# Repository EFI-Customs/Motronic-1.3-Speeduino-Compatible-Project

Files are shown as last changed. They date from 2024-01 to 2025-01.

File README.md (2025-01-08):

# Speeduino Compatible BMW ECU's

This is the main repository containing base maps for various BMW engines utilising the Speeduino Compatible PCB's from EFI Customs.

As well as this, you will find documentation on building your own PCB's.

# Base Maps

It is important to note that these base maps are not intended to be a "ready to go" tune. 

These are purely used as a starting point to get your project going without having to go through the time-consuming process of tweaking every setting.

It is also important to verify your timing with a light before you crank your engine with injectors firing, otherwise you may cause some damage to your motor (not good!). 
These base maps have been preset to be 50deg ATDC (After Top Dead Centre, as opposed to the typical Before Top Dead Centre values used in other kinds of standalone ECU's), which seems to be a typical expected value on a stock M20 running factory single ignition coil. 

Lastly, these base maps have been built under the assumption that a MAX992x based VR Conditioner for the crank sensor. As such, the Trigger Edge is set to RISING. If you are running another type of VR Conditioner or you've converted to Hall Effect then please ensure you have checked this setting before cranking. Remember that if you have switched over to a Hall Effect crank sensor then you need to change jumper configuration on the PCB. There is a jumper configuration table located on the silkscreen underneath where the Arduino mounts.

You can also achieve your own base map by using the Speeduino base maps found here: [Official and user contributed base tunes for Speeduino installations](https://github.com/speeduino/Tunes)

## Motronic 1.3 General Information & Observations
These instructions are designed for the V1.7 Motronic 1.3 Board.
For the Motronic 1.3 compatible ECU, please ensure you have done;

### Air Flow Meter (AFM)
Assuming you are keeping your AFM, unplug the AFM connector and add wires to pins 1 & 4 on the plug and connect them to pins 1 & 4 on the AFM. 
Doing so allows us to utilise the factory intake air temperature sensor. 

The reason we need to unplug pins 2 & 3 is because they go to the External MAP and +5V line on the ECU pins 7 and 12 respectively. 
If you do not do this, you will find that your MAP reading will halve, and you will experience signal noise.

If you intend to delete the AFM, you can instead run any generic intake temperature sensor. A very popular one is an Open Element GM IAT sensor. Again, you can just wire this sensor into the factory AFM harness (pins 1 & 4).

### TPS
If you want to start the car without re-wiring the TPS, simply unplug it and manually enter values in the TPS calibration window to spoof readings. 
However, on a full implementation of this board it is highly recommended to convert to an M50 style TPS.

To convert your TPS to the M50 one you need to do the following:

 - Acquire M50 TPS (Part number 13 63 1 721 456)
 - Acquire M50 TPS Adapter 
 - Swap pins 1 (Brown/Blue) and 2 (Brown) on the factory TPS Connector

### Ignition

If you are running factory ignition and you have the cylinder 1 pulse sensor attached (image link here: https://www.r3vlimited.com/board/filedata/fetch?id=7225671) you need to unplug the sensor from the engine harness. 

The Motronic PCB's support individual coil-on-plug for up to 4 cyl engines (needs Cam Position Sensor retrofitted) and wasted-spark for 6-cyl engines. To retrofit a cam sensor you can re-use the cylinder 1 pulse sensor plug on the engine harness side. A MAX9926 VR Conditioner accepts two inputs (crank + cam).

The principle remains similar for both platforms, but we will cover the most common Wasted Spark conversion for an M20.

There are multiple approaches to converting to Wasted Spark, we'll cover the two easiest:

#### Method 1 - Retain the factory coil wiring (black wire and green wire)
The Motronic 1.3 PCB has an external ignition connector for additional channels, for this method you need to add two wires that go from the Ign 2.1 and 3.1 channels on the connector to the respective coils. 
In total, you will have three ignition channel wires and one +12V (green) wire.
The factory black wire will act as channel 1 ignition, 2.1 (PCB) is channel 2 and 3.1 (PCB) is channel 3.

#### Method 2 - Utilise the external connector exclusively
As the title suggests, we either remove or hide the factory black ignition wire and run the 3 channels exclusively from the external ignition connector on the ECU PCB.

Channel 1.1, 2.1 and 3.1 on the PCB are channels 1,2,3 respectively. 
With this method, we still retain the factory green coil wire to provide switched +12V.

#### Ignition wiring continued
We have used a GM V6 Coil Pack with a gutted and re-wired DFI module.

Reference Delphi Coil Pack Part Number: GN10123

Reference Delphi DFI Module Part Number: CM414

Reference DFI Module wiring guide: https://www.e30zone.net/e30wiki/images/9/9a/Gmgutted.jpg

Another wiring reference image: http://i.imgur.com/Q9WdHVS.png

Use a multimeter to ensure you have connected the respective wires to the appropriate pins on the DFI Module.
+12V should be a shared pin across all three pairs of pins (usually the left pin on each pair)
Then channels 1-3 will be individual pins (i.e. not shared).

Label your coil packs with the cylinders they will supply spark for.

- Channel 1 -> 1-6
- Channel 2 -> 2-5
- Channel 3 -> 3-4

Install the DFI module and run some new ignition leads to your spark plugs.
Connect the new wiring from the DFI module into your Motronic PCB External Ignition Connector.
#### TunerStudio settings
With wasted spark installed, you will need to change a few things in your tune file.

Firstly, you need to go into `"Settings" -> "Trigger Setup"` and change the `Trigger Angle` from `50` to `276`. The M20 has a trigger angle of 84 deg BTDC. 
360 - 84 = 276. **This trigger angle is a starting reference point and shouldn't be your final value until you have verified this with a timing light!!** 
Our 2.9 stroker M20 reads 88 deg BTDC which equates to 272 ATDC trigger angle.

Secondly, go to `"Spark" -> "Spark Settings"` and change `"Spark Output Mode"` to `"Wasted Spark"`.
That's it! Wasted Spark is now ready to go.

### Injection
The factory injector wiring is designed to run in a batched manner. Unfortunately, the Speeduino firmware does not support batched injection. To make this work our base maps use untimed or simultaneous injection. 
This isn't perfect and will likely run rich. Tuning this also becomes rather difficult. 
The best approach for this is to convert our injector wiring to a paired setup.

This process can be done in a way that makes it fully reversible. While it's not necessarily the perfect solution, it worked for us when we needed to revert the injector wiring to meet specific requirements.

Starting with a Series 1 E30 M20 injector harness (this can be done with a series 2 harness, but requires a bit more finesse), we separated all the wires. We routed the brown/yellow wires (cylinders 2, 4, 6) and the brown/white wires (cylinders 1, 3, 5) to a 6-pin Deutsch connector, labeling them 1 through 6 accordingly. A multimeter was used to verify the correct wiring for each injector.

We also separated the temperature sensor wires and connected them to a 4-pin Deutsch connector.

The engine harness requires two 4-pin Deutsch connectors—one for the temperature sensor wires, and another for Injector Channels 1, 2, and 3, along with the injector 12V+ (which typically comes into the from the main relay/DME relay).

Next, it's time to create an adapter. Take a 6-pin Deutsch connector and wire it to match the one on the injector harness. On the other end, merge the injector pairs: cylinders 1 & 6 to Channel 1, cylinders 2 & 5 to Channel 2, and cylinders 3 & 4 to Channel 3. Wire these into a 4-pin Deutsch connector that aligns with the engine harness plug. Lastly, combine all the injector 12V+ wires (these are Red/White) into a single thicker cable (we used 12AWG wire for this) and connect it to the final open port on the 4-pin Deutsch connector.

For the third injector channel, route the wire neatly into the factory harness and run it back to the ECU, where it connects to the 3rd Channel output (bottom left) on the External Injector Connector of the PCB.

This setup gives you a flexible injector harness that can be adjusted as needed. In our case, we created two adapters—one for paired injectors and one for batch firing.

1_diagram

### MAP/Vacuum
Run a vacuum hose from the intake manifold to where your ECU is installed. You can get a T-Piece adapter and run the vacuum hose from between the intake manifold and the fuel pressure regulator.

### Wideband
Install a wideband controller and gauge. One we have used many times before is the Innovate LC-2. This comes with the controller, sensor, gauge and supports two programmable sensor outputs.

Refer to the instruction manual for installation and wiring or inquire with your preferred auto electrician.

For our installation, we have grounded our sensors to the ECU (using the expansion pads located underneath the Arduino) and re-programmed the LC-2's second sensor output to Wideband and wired it to the middle-bottom pin of the black IO connector on the Motronic PCB.

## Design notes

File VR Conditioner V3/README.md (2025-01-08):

This is a design based on the Speeduino V3 VR Conditioner that you can find [here](https://github.com/speeduino/Hardware/tree/main/VR%20Conditioner/Prior%20Versions/v3)

It is electronically identical but has been converted to a KiCAD project and uses smaller footprints for the additional resistors and a revised circuit board package size.

I have provided the KiCAD project files in the KiCAD directory. The Gerber, BOM and Positions files are available so that you may easily order from JLCPCB. Note that the jumper, 2 resistors and empty 8 pin DIP socket will come back as unpopulated when requesting PCB assembly.

This design is released under the [CERN Open Hardware License v2 Strong (CERN-OHL-S)](https://ohwr.org/cern_ohl_s_v2.txt) license. This license is similar to the GPL, however is designed specifically for hardware design files, including PCB layouts and schematics. As the 'strongly reciprocal' version of the CERN OHL is used, you may use, copy, modify and create variations of these designs freely, provided that any changes or variations are also released under this CERN-OHL-S.

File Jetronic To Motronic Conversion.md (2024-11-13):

# Jetronic to Motronic Conversion Guide

This guide is not exhaustive nor definitive, and is aimed for people who have experience with automotive electronics and fabrication.

Please note the conversion from Jetronic to Motronic in this guide does not use factory ignition or injection and you will need to make up your own harnesses for these components.

## Requirements
- High impedance injectors - Jetronic injectors are low impedance and are not directly compatible with most standalone ECU's.
- Crank pulley trigger conversion kit - the factory harness uses two crank position sensors in the bell housing which are not compatible
- Motronic 1.1/1.3 crank position sensor
- Motronic 1.3 female connector (side that connects to the ECU) with fly-leads
- Aftermarket air temperature sensor
- Motronic 1.3 coolant temperature sensor
- **Optional** 3bar fuel pressure regulator upgrade

## Factory wiring
To make this conversion work, we will de-pin or cut wires from the jetronic ECU connector and join them to the M1.3 ECU connector.

Refer to the [ECU Pinouts - E30 Zone Wiki](https://www.e30zone.net/e30wiki/index.php/ECU_Pinouts) for tables and connector diagrams of Jetronic and Motronic 1.3.

The following table will outline Jetronic connector pin numbers and their respective M1.3 connector pin destination

| Description | Jetronic Pin | Jetronic Colour | Motronic/Destination Pin |
| --- | --- | --- | --- |
| Tachometer | C104 Pin 1 | BL/BU | 6 |
| Switched power from main relay | 9 | RD/WT | 37 |
| AFM Air temp - pin 1* | 8 | GR/VI | 44 |
| Coolant temp input | 10 | BR/RD | 45 |

*We will also be disconnecting the AFM and plumbing an aftermarket intake temperature sensor. You may optionally delete the AFM entirely.

You will also need to join all of the ground wires accordingly.

## Custom wiring

### Main Relay + Fuel Pump Relay

Since the Jetronic system does not have a main relay, we will need to wire one in.
There's a few different ways to do this but we will simplify it.

Using the [DME - E30 Zone Wiki](https://www.e30zone.net/e30wiki/index.php?title=DME#Operation) article we can get the neccessary wiring information for the main relay.
In short:
- DME Relay pins 30 and 86 are to be connected to constant, unfused 12V
- DME Relay pin 85 goes to pin 36 of the M1.3 harness
- Ignition being turned on should provide 12V to pin 27 on M1.3 harness, which should ground pin 36 on M1.3 harness thus activating the DME relay
- DME Relay pins 30 and 87 bridge upon activation, supplying power to the fuel pump, injectors and to pin 37 of the M1.3 harness (which we have outlined in the previous table)

With all of this in mind, to simplify the setup we don't need:
- Switched 12V to pin 27 on M1.3 harness
- No grounding of pin 36 on M1.3 harness
- Main relay powering the fuel  (though you can do this if you wish)

We can also remove the old 7 pin fuel pump relay, and re-use some of the wires for our new relays.
Namely, we can cut the following wires from the 7-pin relay:
- pin 15 - Switched 12v
- pin 31 - Ground
- Pin 30 - Unfused 12v
- Pin 87 - 12v to fuel pump

Using the above wires, we can make up the main relay using pins 15, 31 and 30 to pins 85, 86 and 30 respectively. Then a new wire going from pin 87 on the relay to pin 37 on the M1.3 harness and a split that provides injectors with a common 12V. Optionally, you may also use another split from DME relay pin 87 to activate the fuel pump relay.
maain-relay

Likewise with the fuel pump relay, we can make up relay using pins 15, 31 and 30 to pins 85, 86 and 30 respectively.
Lastly, wire pin 87 from the 7 pin relay to pin 87 on the new relay to provide the fuel pump with 12v.
fuel-relay (1)

### Air Temperature Sensor

We will need to plumb an air temperature sensor into the intake system. The easiest rule of thumb to stick to, is to plumb the sensor approximately where the AFM is located.
Majority of aftermarket sensors work on the same principle of resistance comparison from a 5v reference. Pin 8 from the jetronic harness will go into the signal pin on the temperature sensor, the ground pin on the sensor can be supplied from a ground wire on the engine harness. Note that pin 8 on the jetronic harness goes to pin 1 on the AFM connector.

### Coolant Temperature Sensor
This is a simple replacement procedure which requires the blue coolant sensor for a M1.3 system.

### Crank Trigger wheel

The trigger wheel will require welding on to the crank pulley. You will then need to install the crank sensor mount to the engine block, and fasten the crank position sensor to it. Run the CPS wire along the front timing cover to underneath the intake manifold.

Below is a reference image of where to position the trigger wheel relative to the original timing marks where the gap in green signifies the missing teeth on the trigger wheel.


### Crank position sensor

Using some 2 core shielded wire:
- Wire up to a 3 pin EV1 connector to interface with the crank position sensor
- From the EV1 connector, join the wire to the Motronic 1.3 harness as outlined in the table below

| CPS Pin | Description | Wire Colour | Motronic 1.3 Pin |
| --- | --- | --- | --- |
| 1 | VR + | Black | 47 |
| 2 | VR - | Yellow | 48 |
| 3 | Shield Gnd  | N/A | Gnd |

### Injectors

There's many to choose from and this greatly varies on the application and requirements of the vehicle.
For vehicles maintaining natural aspiration can use M20B25 blue injectors, or M50B25 green injectors. For those intending to squeeze out more power (such as high compression strokers) may look at M52B28 pink injectors as a viable option.

All of the aforementioned injectors maintain the same dimensions as the stock injectors and directly clip into the fuel rail requiring no further modification.

To maintain OEM-like wiring layout, you can feed injectors with 12V from the main relay. The trigger/signal wires can be run directly to the ECU's external injector connector.

### Ignition

Much like the injector wiring, the ECU has an external connector for ignition trigger/signal wires.

Depending on which ignition coils you choose to utilise, the wiring may vary slightly. But generally, you will need to provide a switched 12V feed to the coil pack/packs and a signal input from the ECU's external ignition connector. Some coil packs may require additional grounding. In most cases, grounding to the rocker cover is acceptable.

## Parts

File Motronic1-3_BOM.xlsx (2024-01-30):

ID | Name | Designator | Footprint | Quantity | DigiKey.com
1 | LM2940T-5.0/NOPB | U1 | TO-220-3 | 1 | LM2940T-5.0/NOPB
2 | ISL9V5036P3 | Q1,Q2,Q3,Q4,Q5,Q6 | TO-220(TO-220-3) | 6 | ISL9V5036P3-F085-ND
3 | STP75NS04Z | Q7,Q8,Q9,Q10,Q11,Q12,Q13 | TO-220(TO-220-3) | 7 | 497-5981-5-ND
4 | motronic 55 pin plug | P1 | MOTRONIC 55 | 1
5 | ARDUINO-MEGAPRO-5V | U3 | ARDUINO_MEGA-PRO-5V - REV - NAS | 1 | 1050-1018-ND
6 | ULN2003A_C93000 | U5 | DIP-16 | 1 | 497-2344-5-ND
7 | SP721APP | U7 | DIP8-2.54-10.9X6.6MM | 1 | F2720-ND
8 | 1N5818RLG | D1,D2,D4 | DO-35F | 3 | 1N5818-TPCT-ND
9 | 14D220K | U2 | AXIAL-0.4 | 1 | P7307-ND
10 | 10uF | C1 | CAP-TAN-S2.5 | 1 | 478-1842-ND
11 | 47uF | C3 | CAP-TAN-S2.5 | 1 | 399-3652-ND
12 | 1N5919BG | D3 | DO-41F | 1 | 1N5919BGOS-ND
13 | 1K | R1,R3,R4,R10,R13,R16,R19,R20,R21,R22,R23,R36,R37,R38,R39,R43,R57,R65 | AXIAL-0.3 | 22 | 1.00KXBK-ND
14 | 10k | R2,R5,R6,R7,R61,R64 | AXIAL-0.3 | 6 | 10.0KXBK-ND
15 | 4.7nF | C5 | CAP-0.2 | 1 | 399-4243-ND
16 | 680R | R8,R11,R14,R17 | AXIAL-0.3 | 4 | A105963CT-ND
17 | LED-3MM | LED1,LED2,LED3,LED4,LED5,LED6,LED7,LED8 | LED-3MM/2.54 | 8 | 160-1139-ND
18 | 1N4448 | D5,D6,D7,D8 | DO-35 | 4 | 1N4004-TPMSCT-ND
19 | 100k | R9,R12,R15,R18,R24,R25,R26,R27 | AXIAL-0.3 | 8 | 100KXBK-ND
20 | 2.49k | R28,R29,R30,R31,R44,R46,R59 | AXIAL-0.3 | 7 | 2.49KXBK-ND
21 | 160R | R32,R33,R34,R35 | AXIAL-0.3 | 4 | 160YCT-ND
22 | 1uF | C6,C7,C11,C24 | CAP-0.2 | 4 | 399-4390-ND
23 | 0.01uF / 10nf | C8,C9,C12,C25 | CAP-0.2 | 4 | 399-4206-ND
24 | 470R | R40,R42,R45,R48,R51,R54,R58 | AXIAL-0.3 | 7 | RNF14FTD470RCT-ND
25 | 0.33uF / 330nf | C10,C23 | CAP-0.2 | 2 | 478-5120-ND
26 | 3.9k | R41 | AXIAL-0.3 | 1 | 3.9KADCT-ND
27 | 0.1uf | C2,C4,C13,C15,C17,C19,C21 | CAP-0.2 | 7 | 399-9879-1-ND
28 | 0.22uf | C14,C16,C18,C20,C22 | CAP-0.2 | 5 | BC2678CT-ND
29 | DS1001-01-08BT1NSF6X-JKB | SK1 | DIP-8 | 1 | AE10011-ND
30 | 7.5k | R56 | AXIAL-0.3 | 1 | 7.5KQBK-ND
31 | 2N2222A | Q14,Q15 | TO-92(TO-92-3)-2.54 | 2 | 2N2222 PBFREE
32 | 1N4004 | D9,D12 | DO-35F | 2 | 1N4004-TPMSCT-ND
33 | MPX4250AP | U4 | MPX4250AP_BOTTOM | 1 | MPX4250AP-ND
34 | MPXH6115A6U | U14 | SSOP-8_MPXH | 1 | MPXH6115A6U-ND
35 | 4N35 | U10 | DIP-6 | 1 | 160-1304-5-ND
36 | 4.7k | R60 | AXIAL-0.3 | 1 | 4.7KQBK-ND
37 | 2.2k | R62,R63 | AXIAL-0.3 | 2 | 2.2KQBK-ND
38 | TC4424EPA | U8,U9 | DIP-8 | 2 | TC4424EPA-ND
39 | IO Header | IO |  | 1 | WM1815-ND
40 | IO Connector |  |  | 1 | WM1785-ND
41 | IO Connector Contact |  |  | 6 | WM1837CT-ND
42 | INJ/IGN Header | INJ_OUT,IGN_OUT |  | 2 | WM1353-ND
43 | INJ/IGN Connector |  |  | 2 | WM3702-ND
44 | INJ/IGN Connector Contact |  |  | 12 | WM3282CT-ND
45 | 2.54mm Male Pin Header |  |  | 4 | S1012EC-40-ND
 | Optional Active Clutch HIGH Circuit | Please note, don't combine low and high clutch circuits. Choose which one suits your application best
 | Optional Active Clutch LOW Circuit

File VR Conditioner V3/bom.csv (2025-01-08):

Designator | Footprint | Quantity | Value | LCSC Part #
C1 | 0805 | 1 | CC0805ZRY5V9BB104
C2 | 0805 | 1 | CC0805KRX7R9BB103
C3 | 0805 | 1 | CC0805KKX7R7BB105
C4, C5 | 0805 | 2 | CC0805KRX7R9BB102
MAX9926 | 21-0055H_16_MXM | 1 | MAX9926UAEE+T
R11, R13, R7, R9 | 0805 | 4 | RC0805JR-0710KL
R4, R6 | 0805 | 2 | RC0805FR-071KL

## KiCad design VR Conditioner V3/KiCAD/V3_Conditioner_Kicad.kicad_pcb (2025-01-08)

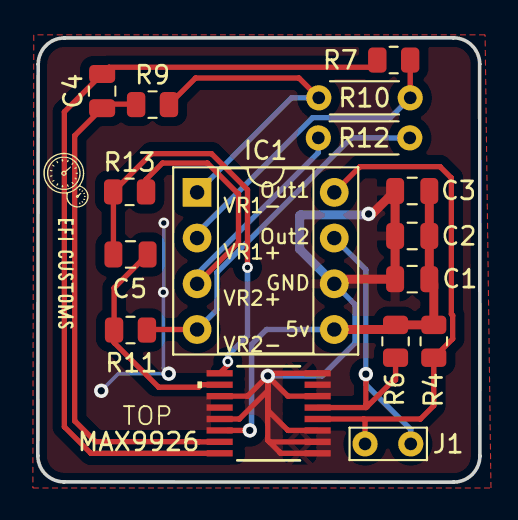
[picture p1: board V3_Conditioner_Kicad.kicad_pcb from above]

Board: 2 copper layers, 24.6 x 24.7 mm, 16 parts (0 on the bottom side), 12 nets.

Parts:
C1: CC0805ZRY5V9BB104; C_0805_2012Metric
C2: CC0805KRX7R9BB103; C_0805_2012Metric
C3: CC0805KKX7R7BB105; C_0805_2012Metric
C4, C5: CC0805KRX7R9BB102; C_0805_2012Metric
IC1: DIP-8_W7.62mm_Socket
J1: Jumper_2_Open; TestPoint_Bridge_Pitch2.54mm_Drill0.7mm
MAX9926: MAX9926UAEE+T; 21-0055H_16_MXM
R4, R6: RC0805FR-071KL; R_0805_2012Metric
R7, R9, R11, R13: RC0805JR-0710KL; R_0805_2012Metric
R10, R12: 4.7k; R_Axial_DIN0204_L3.6mm_D1.6mm_P5.08mm_Horizontal

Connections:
+5V: C1.1, C2.1, C3.1, IC1.5 (+5V), MAX9926.14, R4.1, R6.1
GND: C1.2, C2.2, C3.2, IC1.6 (GND), MAX9926.1, MAX9926.2, MAX9926.3, MAX9926.6, MAX9926.8, MAX9926.11, MAX9926.13
unnamed: C4.1, MAX9926.16, R7.1
unnamed: C4.2, MAX9926.15, R9.1
unnamed: C5.1, MAX9926.10, R11.1
unnamed: C5.2, MAX9926.9, R13.1
Output1: IC1.8 (Output_1), J1.1 (A), MAX9926.4, R4.2
Output2: IC1.7 (Output_2), J1.1 (A), MAX9926.5, R6.2
VR1+: IC1.2 (VR1+), R7.2, R10.1
VR1-: IC1.1 (VR1-), R9.2, R10.2
VR2+: IC1.3 (VR2+), R12.2, R13.2
VR2-: IC1.4 (VR2-), R11.2, R12.1

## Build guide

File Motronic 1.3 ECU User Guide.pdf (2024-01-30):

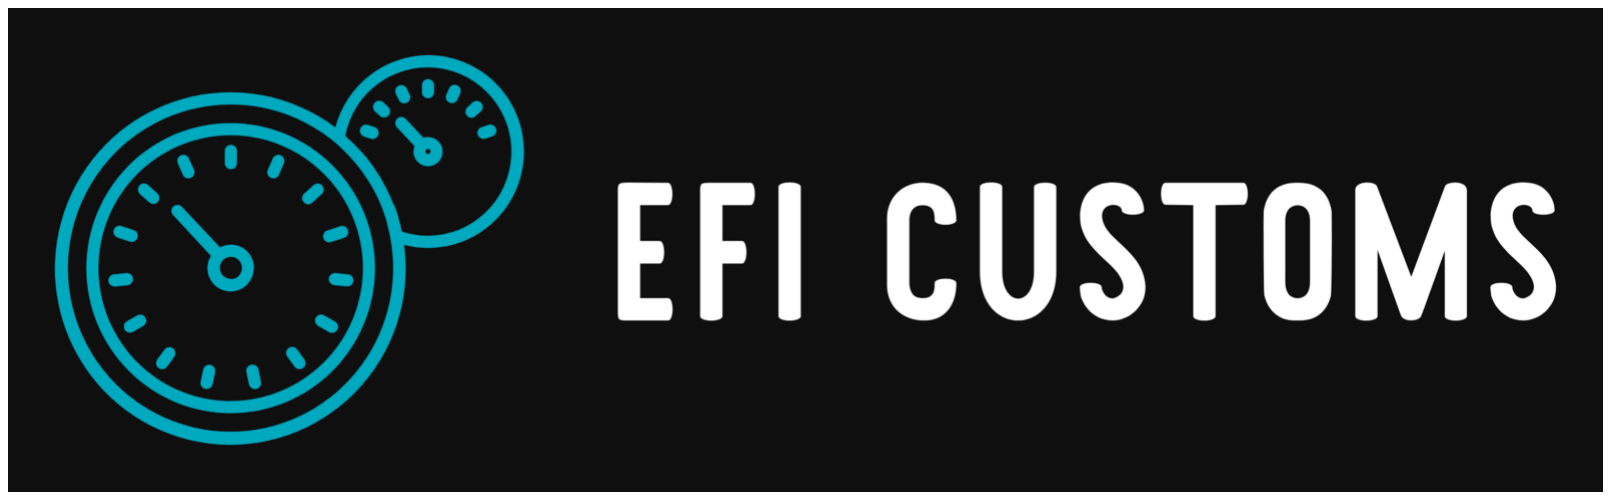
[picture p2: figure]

# Speeduino Compatible Motronic 1.3 ECU

## User Guide

Speeduino Compatible Motronic 1.3 ECU-----------------------------------------------------------------------------------------------------------------------1 User Guide--------------------------------------------------------------------------------------------------------------------------------------------------------1 Disclaimer---------------------------------------------------------------------------------------------------------------------------------------------------------2 Before connecting the ECU to your vehicle-------------------------------------------------------------------------------------------------------------- 3 Cylinder ID Sensor--------------------------------------------------------------------------------------------------------------------------------------- 3 AFM----------------------------------------------------------------------------------------------------------------------------------------------------------3 TPS---------------------------------------------------------------------------------------------------------------------------------------------------------- 4 Injectors-----------------------------------------------------------------------------------------------------------------------------------------------------5 Ignition------------------------------------------------------------------------------------------------------------------------------------------------------ 5 External Connectors--------------------------------------------------------------------------------------------------------------------------------------------6 ECU Connector Pinout-----------------------------------------------------------------------------------------------------------------------------------------8 ECU Setup------------------------------------------------------------------------------------------------------------------------------------------------------ 10 Engine Constants---------------------------------------------------------------------------------------------------------------------------------------10 Injector Characteristics-------------------------------------------------------------------------------------------------------------------------------- 12 Trigger Setup-------------------------------------------------------------------------------------------------------------------------------------------- 13 Trigger Angle---------------------------------------------------------------------------------------------------------------------------------------------14 Spark and Dwell Settings----------------------------------------------------------------------------------------------------------------------------- 15 Idle Settings---------------------------------------------------------------------------------------------------------------------------------------------- 16 Calibration-------------------------------------------------------------------------------------------------------------------------------------------------------17 TPS Calibration----------------------------------------------------------------------------------------------------------------------------------------- 17 Temperature Sensor Calibration-------------------------------------------------------------------------------------------------------------------- 18 Wideband Calibration----------------------------------------------------------------------------------------------------------------------------------20 Voltage Reading Calibration------------------------------------------------------------------------------------------------------------------------- 20 Noteworthy Miscellaneous Items-------------------------------------------------------------------------------------------------------------------------- 21 Getting Started with TunerStudio------------------------------------------------------------------------------------------------------------------- 21 Firmware Updates-------------------------------------------------------------------------------------------------------------------------------------- 21 Relay Outputs------------------------------------------------------------------------------------------------------------------------------------------- 21 USB Connection---------------------------------------------------------------------------------------------------------------------------------------- 21 Bluetooth--------------------------------------------------------------------------------------------------------------------------------------------------21

For more detailed information, troubleshooting, and advanced tuning options, consult the Speeduino documentation (wiki.speeduino.com) and user community (speeduino.com/forum/).
Note: This guide is intended for informational purposes only. Always consult the Speeduino documentation and seek professional assistance if you encounter difficulties during installation or tuning. EFI Customs does not take any responsibility for any damage that can occur to electronics, wiring or engines. By using our ECU you accept the risks associated with incorrect configuration and user error.

## Disclaimer

By purchasing and using the Speeduino Compatible Motronic 1.3 ECU ("the Product") from EFI Customs, the buyer/user ("You") agrees to and understands the following:

1. Proper Use and Installation: The Product is designed for specific purposes and must be installed, configured, and used according to the manufacturer's guidelines and instructions. You are solely responsible for ensuring that the Product is correctly installed and configured.
2. No Liability for Misconfiguration or Damage: EFI Customs assumes no responsibility or liability for any damages, malfunctions, or performance issues related to the Product which are a result of misconfiguration, improper installation, misuse, or any alterations made to the Product by the user or a third party.
3. Vehicle and Property Damage: EFI Customs is not responsible for any damage caused to vehicles, engines, or any other property as a result of using the Product. It is your responsibility to monitor the performance of your vehicle or property and ensure that the Product is functioning as intended.
4. Warranty Limitations: This disclaimer does not affect any manufacturer warranties that may come with the Product. However, EFI Customs' liability is strictly limited to the repair, replacement or refund of the Product, subject to applicable laws and any terms and conditions of sale.
5. User Responsibility: It is your responsibility to frequently check for updates, notices, and instructions related to the Product. Ignorance or unawareness of any guidelines, updates, or advisories does not exempt you from the responsibilities set out in this disclaimer.

By continuing with the purchase and/or use of the Product, you acknowledge that you have read, understood, and agreed to the terms outlined in this disclaimer.

For more detailed information, troubleshooting, and advanced tuning options, consult the Speeduino documentation (wiki.speeduino.com) and user community (speeduino.com/forum/).
Note: This guide is intended for informational purposes only. Always consult the Speeduino documentation and seek professional assistance if you encounter difficulties during installation or tuning. EFI Customs

Welcome to the world of enhanced engine control with your Speeduino compatible ECU! This user guide will help you get your ECU up and running smoothly with your BMW Motronic 1.1/1.3 wiring harness. Please follow these steps carefully to ensure a successful installation.

## Before connecting the ECU to your vehicle

While the ECU you have purchased is designed to be as easy-to-install as possible, the Motronic wiring harness is quite outdated and the ECU has been built with upgradeability in mind. There are a few pins on the ECU that are used for new functionality, and a few things that are recommended to be done first.

For more details, please check out our GitHub documentation by following this QR code:

### Cylinder ID Sensor

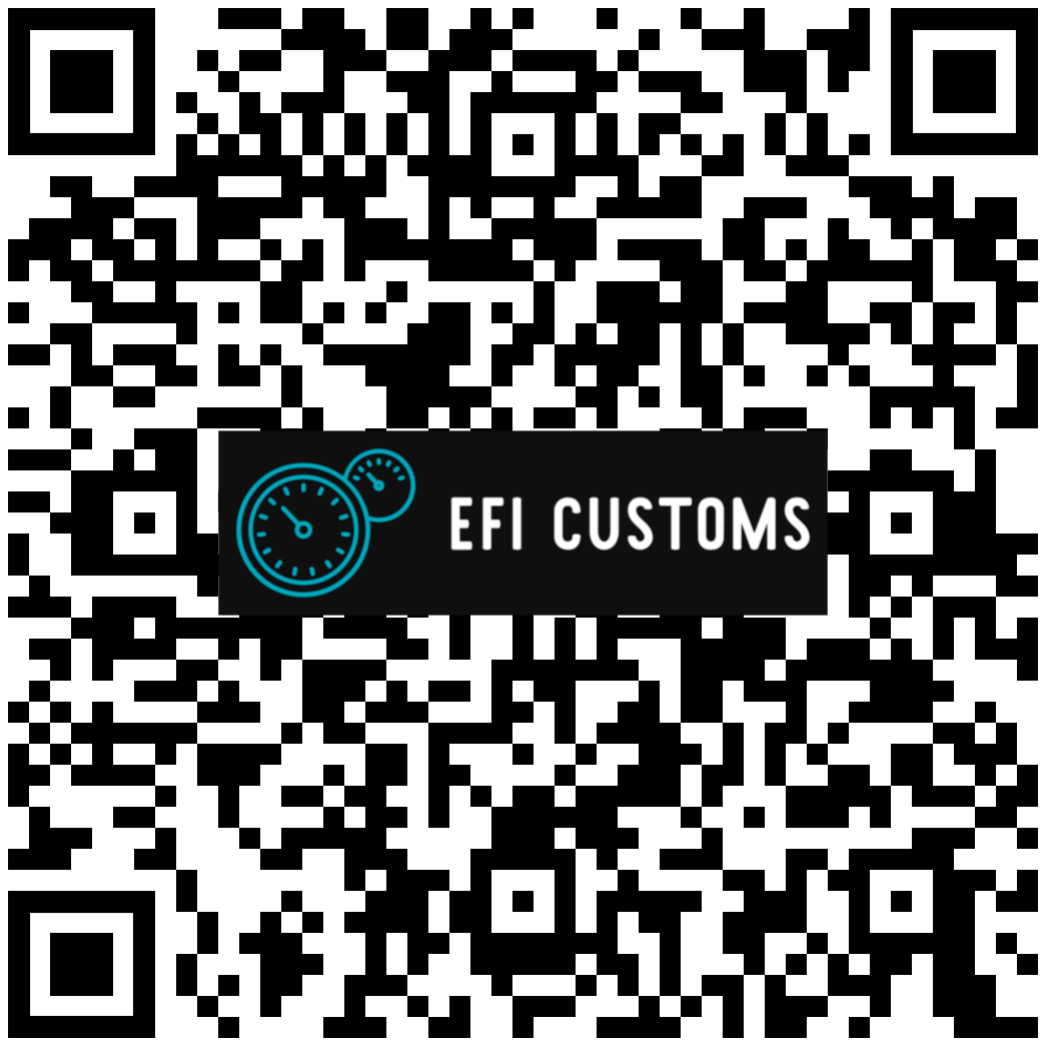
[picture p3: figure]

If your engine has a cylinder ID sensor - Pins 8 and 31 on the engine harness ECU connector socket, and its plug is usually positioned right next to the Crank Position Sensor plug in the engine bay - disconnect it. The ECU has repurposed this connector for a potential Camshaft Position Sensor which unlocks sequential injection/ignition (4 cylinder engine only), this is covered in External Connectors on page 6.

### AFM

If you are intending to not remove the AFM from your engine please disconnect the AFM Plug and either de-pin the two middle pins on the AFM Plug and re-connect or run two new wires from pins 1 & 4 from the plug to the AFM.

For more detailed information, troubleshooting, and advanced tuning options, consult the Speeduino documentation (wiki.speeduino.com) and user community (speeduino.com/forum/).
Note: This guide is intended for informational purposes only. Always consult the Speeduino documentation and seek professional assistance if you encounter difficulties during installation or tuning. EFI Customs

The ECU has repurposed the two middle AFM Plug pins to run an External MAP sensor. Please refer to ECU Connector Pinout on page 8 - these two pins correlate to Pins 7 and 12 on the ECU connector.

In most cases, removing the AFM is the best option as it removes an airflow restriction. In place of the internal AFM temperature sensor, it’s suggested to use something like the GM Open Element IAT sensor (part number 25036751) and connect its pins/wires to pins 1 & 4 of your existing AFM Plug. This is purely a recommendation and you can run any two-wire air temperature sensor that has published calibration tables.

### TPS

The original TPS on a Motronic 1.3 harness is actually a 3 position switch and cannot be repurposed for a variable position sensor.
It is recommended to use an M50 TPS (Part number: 13 63 1 721 456).
Using a TPS enables you to utilise features such as Flood Clearing, Conditional map switching, Launch Control and Flat shifting, Alpha-N tuning as well as many others.
To complete the wiring portion of the M50 TPS conversion, you will need to swap pins 1 (Brown/Blue) & 2 (Brown) on the TPS Plug. This can be done by pulling the rubber boot back on the TPS Plug to expose the wires. You can either use a de-pinning tool to switch them or cut and crimp them.
There are 3 wires in total and their purpose is as follows on the factory ECU:
Pin | Wire Colour | Purpose
1 | Brown/Blue | Closed Throttle
2 | Brown | Ground
3 | Brown/Black | Wide Open Throttle

The Speeduino Motronic 1.3 ECU is expecting the following pinout:

Pin | Wire Colour | Purpose
1 | Brown | Ground
2 | Brown/Blue | Signal (Previously Closed Throttle)
3 | Brown/Black | 5v ref (the ECU already caters for this so no modification is required)

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

### Injectors

In all Motronic 1.3 engines, the injectors are configured in a batched manner. Speeduino firmware does not support batched injection so if you don’t wish to modify your wiring, configure your Injector Staging in the Engine Constants setting in TunerStudio to be simultaneous and 1-3 squirts per engine cycle.You may need to play around with the squirts per cycle value depending on the observed behaviour of the engine after adjusting the fuel table. This will roughly mimic the stock ECU behaviour but you may find it more difficult to tune your fuel map. This is because the injector firing is based on the TDC of cylinder 1. Due to this the first cylinder receives best fuel timing and the rest will occur at various stages which will impact fuel consumption/efficiency. Quite often you will find that the vehicle will run rich.

The M40 motor requires swapping wiring of injectors 3 and 4 for paired injection to function correctly. The factory ECU pairs odd and even cylinders in separate channels but we want to configure our injectors to be opposing each other to match the firing order (1,3,4,2).
If you are upgrading to semi/sequential the ECU can accommodate individual injector control by utilising the external connector (camshaft sensor is required for full sequential).

On 6 cylinder motors, the injection is batched in two channels. Our recommendation is to convert your injector wiring to be three pairs of two injectors (usually 1&6, 2&5, 3&4 but do your own research on your preferred approach). This configuration is covered in our GitHub documentation which you can access via the QR code on the third page of this guide.

### Ignition

The Speeduino ECU supports distributor ignition which requires no wiring modification. In the Engine Constants section of TunerStudio you simply need to define how many cylinders you have. If you are retaining your distributor ignition system, you will have to set your trigger angle to 50 degrees After Top Dead Center on 6 cylinder models.

Though it is recommended to verify your trigger angle with a timing light.

For wasted spark configuration and wiring, check the GitHub documentation which you can access via the QR code on the third page of this guide.

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

## External Connectors

Your ECU has a total of 5 connectors located on the sides and back side.

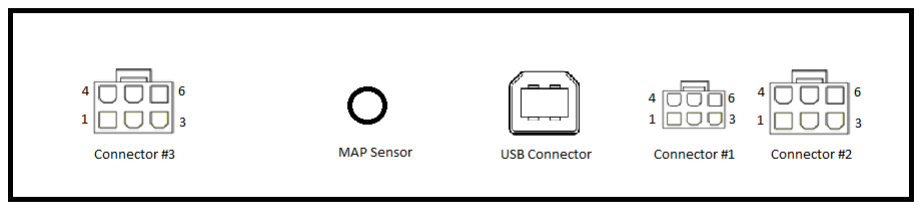
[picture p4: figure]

Please note: The connectors may have physical numbering on the plastic, please disregard this numbering and refer to the numbering of the above diagram and below table.

Connector #1 | Connector #2 | Connector #3
Pin | Purpose
1 | Clutch Input
2 | Wideband Input
3 | Spare output 3
4 | Flex fuel Input
5 | Spare output 4
6 | Spare output 2
Pin | Purpose
1 | Injector 3 Output
2 | Injector 2 Output
3 | Injector 1 Output
4 | Fan Output
5 | Boost Output
6 | Injector 4 Output
Pin | Purpose
1 | Ignition 3.2/4 Output
2 | Ignition 2.1 Output
3 | Ignition 1.1 Output
4 | Ignition 3.1 Output
5 | Ignition 2.2 Output
6 | Ignition 1.2 Output

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

Engine Cylinder Count | Ignition Type | Outputs
4 | Single Channel | 55 pin ECU connector pin 1
4 | Wasted Spark | Channel 1 (cyl 1,4) -> 1.1 Channel 2 (cyl 2,3)-> 2.1
4 | Wasted COP/Semi Seq | Cylinder 1 -> 1.1 Cylinder 2 -> 2.1 Cylinder 3 -> 2.2 Cylinder 4 -> 1.2
4 | Sequential (needs cam input) Solder Joint 5 (SJ5) needs pins 1 and 2 bridged | Cylinder 1 -> 1.1 Cylinder 2 -> 3.1 Cylinder 3 -> 3.2/4 Cylinder 4 -> 2.1
6 | Single Channel | 55 pin ECU connector pin 1
6 | Wasted Spark | Channel 1 (cyl 1,6) -> 1.1 Channel 2 (cyl 2,5) -> 2.1 Channel 3 (cyl 4,3) -> 3.1
6 | Wasted COP Solder Joint 5 (SJ5) needs pins 2 and 3 bridged | Cylinder 1 -> 1.1 Cylinder 2 -> 2.1 Cylinder 3 -> 3.1 Cylinder 4 -> 3.2 Cylinder 5 -> 2.2 Cylinder 6 -> 1.2

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

## ECU Connector Pinout

Pin | Purpose | Pin | Purpose
1 | Ignition Coil Output (Channel 1 - 1.1) | 18 | Battery +12V
2 | Ground | 19 | Ground
3 | Fuel Pump Relay Control | 20 | N/A
4 | Idle Out | 21 | N/A
5 | N/A | 22 | Idle Out
6 | Tachometer Output | 23 | N/A
7 | External Map Signal In | 24 | Ground
8 | Cam Hall Sensor Signal In | 25 | N/A
9 | N/A | 26 | Ground
10 | N/A | 27 | Ignition signal from key
11 | N/A | 28 | N/A
12 | +5V Rail | 29 | Vehicle Speed Input from cluster->JP1
13 | N/A | 30 | N/A
14 | Ground | 31 | Cam Hall Sensor Power
15 | Check Engine Light | 32 | N/A
16 Injector Channel 1 Out (Factory Cyl | 1,3,5) | 33 N/A
17 Injector Channel 2 Out (Factory Cyl | 2,4,6) | 34 N/A

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

35 | N/A | 46 | N/A
36 | DME Relay Output | 47 | Crank In +
37 | 12V In | 48 | Crank In -
38 | N/A | 49 | N/A
39 | N/A | 50 | N/A
40 | N/A | 51 | N/A
41 | AC In Idle Up Signal | 52 | +5V
42 | N/A | 53 | TPS Signal
43 | N/A | 54 | N/A
44 | Intake Air Temperature In | 55 | N/A

45 Coolant Temperature In

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

## ECU Setup

The ECU you have received has a standard Speeduino base tune applied to it so that all the values are within a normal range. This is usually enough of a starting point, but we also have M20 base tunes available by using the QR code on page 3.
Please note that a base tune is not designed to immediately fire up your engine and drive. These are merely used for accelerating your configuration and you should do your due diligence to double check all values before attempting to start your car.
While you’ve got the ECU disconnected from a car, use this opportunity to configure all of your settings beforehand.

### Engine Constants

Before starting the engine for the first time, you need to configure your Engine Constants. Click on Settings -> Engine Constants

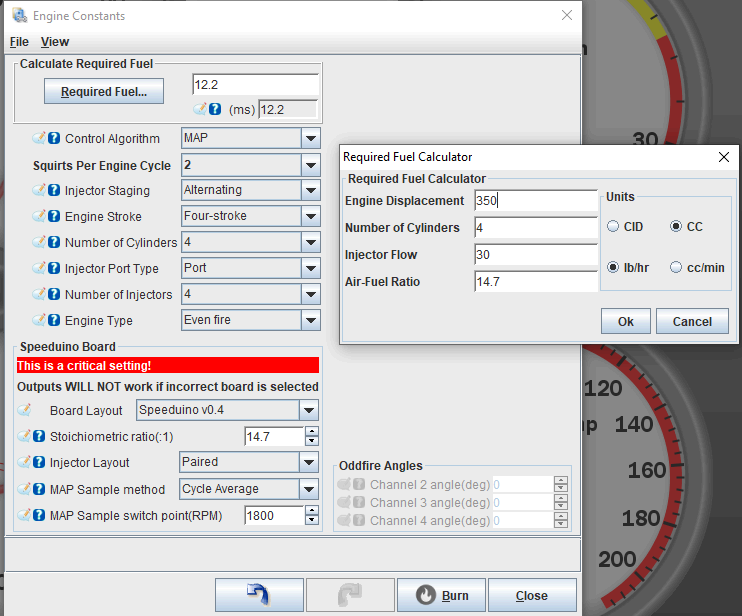
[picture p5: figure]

Before performing the Required Fuel calculation, please populate/update everything else first.

From here you can configure what Load Control Algorithm you want to use. This is where you can change it from the standard MAP to TPS for Alpha-N or Intake MAP/Exhaust MAP. The first two are the most common control algorithms.

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

Injector Staging will determine how to trigger injector signals. If you have set it to Simultaneous then the injector layout section below will be ignored.

Number of cylinders and number of injectors will determine how many signals to fire per single engine rotation so ensure this is set correctly to prevent potential engine damage.

The remainder of the settings are self explanatory and have helpful tooltips (click on the question mark icon for more information).

The Speeduino Board setting is very critical. In the case of the Motronic 1.3 ECU you have purchased, the board layout should be set to Speeduino v0.4.

Stoichiometric ratio should match what you’ve configured in the Required Fuel section.

Injector layout as we’ve mentioned previously will stay in paired mode unless you have specifically wired up your vehicle for semi/sequential injection.
It should be noted that semi-sequential injector layout requires each individual injector wired into the ECU but the firmware will run them in a paired manner.

MAP Sample method can be set to Cycle Average for most vehicles. Vehicles with ITB’s commonly use Cycle Minimum if utilising a mixed TPS/MAP fuel map.
MAP Sample switch point can stay at the default 1800 RPM value. This setting will get instantaneous values from the MAP sensor which tends to help getting a smoother idle.

Lastly, select Required Fuel which will open a pop-up as shown above. In this pop-up you can populate the specific details about your engine displacement, cylinder count, injector flow etc. Populate your relevant details and click Ok. This will recalculate your required fuel and you should see the (ms) number change.

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

### Injector Characteristics

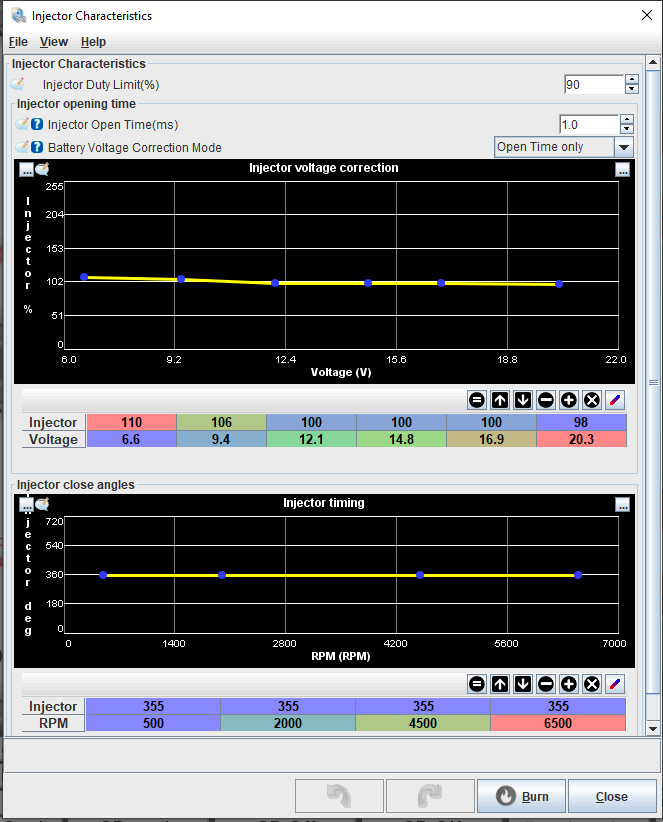
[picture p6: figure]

Injector Open Time is identical to terms such as dead time and latency. So enter the dead time of your injectors and provide the voltage correction.
To view the table cells, click on the three-dot icon on the top right of each respective graph.

Unless you know the dead times of your injectors, for stock M1.3 injectors you can provide a value of 1.0ms and a voltage correction table of:
Injector % | 255 | 201 | 133 | 91 | 60 | 37
Voltage | 7.0 | 8.0 | 10.0 | 12.0 | 14.0 | 16.0

The above table shows values that offer a starting point for most setups.

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

### Trigger Setup

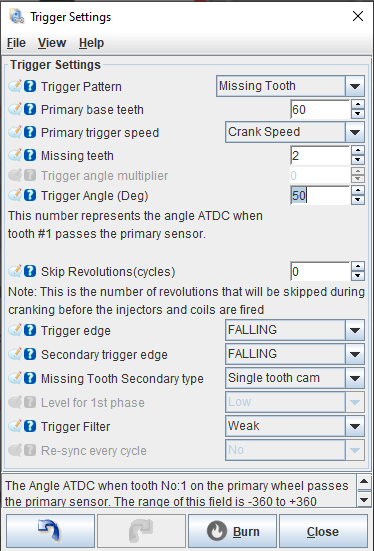
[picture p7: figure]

For Motronic 1.3 engines your:
Trigger Pattern should be Missing Tooth,
Primary base teeth set to 60 and Missing teeth set to 2.
Primary trigger speed is set to Crank Speed.
Trigger Angle is covered in the section below.
Trigger Edge for most VR sensors is FALLING, this includes the factory VR sensors on Motronic 1.3 engines.
Secondary trigger edge, Missing Tooth Secondary Type are both there for the optional camshaft sensor.

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

Trigger Filter is used to reduce any potential interference that can arise either from a noisy wire, or an out of shape trigger wheel. With the licensed version of TunerStudio you can use the high speed logger to detect the Trigger Wheel signal and determine if filtering is required.

### Trigger Angle

You can perform this step before or after commencing your conversion to the standalone ECU. Though this is easier to do with your new ECU.
In TunerStudio software click on the Spark tab -> Spark Settings and in the Locked timing section use the first dropdown to toggle locked timing and in the text box below it, set the degrees to 0. Ensure that Cranking advance Angle is also set to 0.

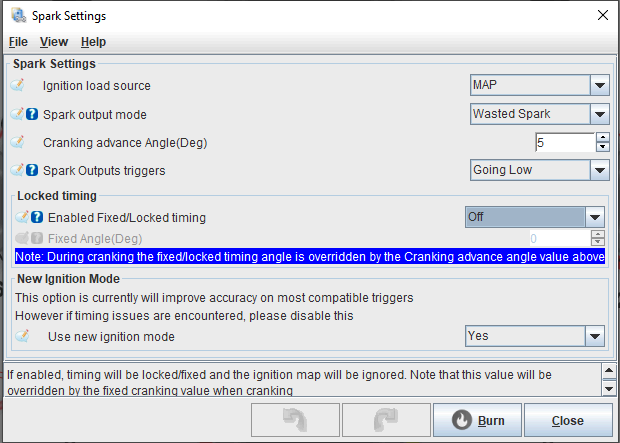
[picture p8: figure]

Next, remove your fuel relay and/or disconnect the injectors so we only trigger sparks, we don’t want to accidentally damage anything due to wrong timing values.
Using a timing light, verify the trigger angle of your motor in degrees before top dead center.

Speeduino trigger angle is defined in degrees AFTER TOP DEAD CENTER, this is unlike other ECU’s such as the Megasquirt that define in degrees BEFORE TOP DEAD CENTER.

Please ensure you’re subtracting the measured trigger angle from 360 to get your ATDC value. If using distributor ignition on a 6 cylinder engine the trigger angle on Speeduino is typically set to 50 ATDC, and on wasted spark this value can vary between 272-278 ATDC.
M40’s are typically near 244 degrees ATDC.

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

### Spark and Dwell Settings

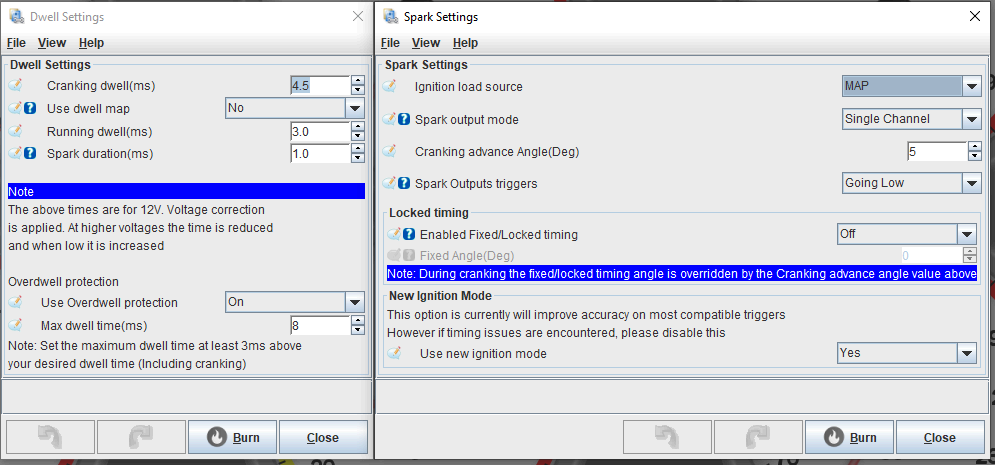
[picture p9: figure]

Go into Spark Settings. In TunerStudio software click on the Spark tab -> Spark Settings. Ignition load source should usually match the Control Algorithm defined in the Engine Constants on page 10.
If you’re running a factory distributor, Spark Output mode should be set to Single Channel. If you’re running wasted spark ignition, Spark Output mode should be set to Wasted Spark. Cranking advance Angle depends on your engine, and can vary between 5-15 degrees. Spark Output trigger is almost always Going Low on Speeduino ECU’s. This depends on the coils you use. BMW Coils up to and including M54 engines will use this setting. If you are using other coils, then please do your research before burning this setting to prevent damaging your coils.
Use new ignition mode should be set to Yes

Now let’s go into Dwell Settings. In TunerStudio software click on the Spark tab -> Dwell Settings.
A stock Motronic 1.3 coil pack can safely run at 2-3ms of dwell.
Cranking can be set to 3ms, running at 2-2.5ms and a duration of 1ms.
Overdwell protection should be on and set to roughly 5-6ms depending on your dwell settings.

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

### Idle Settings

Using a factory Motronic 1.3 ICV the following settings can be used:

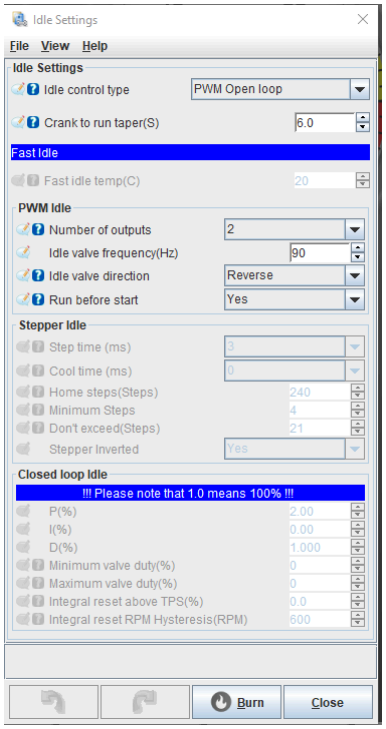
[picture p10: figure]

You may need to switch the Idle valve direction from reverse to normal. This isn’t going to damage anything.

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

## Calibration

### TPS Calibration

To calibrate the TPS, on the top of TunerStudio click on the Tools tab -> Calibrate TPS.

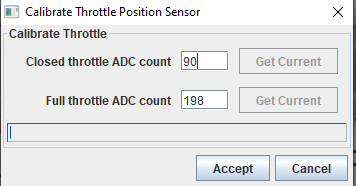
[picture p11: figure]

To correctly calibrate the TPS, firstly depress the throttle pedal and click on Get Current on the Closed throttle ADC count section. Then press the throttle pedal all the way down and click on Get Current on the Full throttle ADC count. Click Accept and (if you have used the standard TunerStudio dashboard) you should now see the TPS gauge move around between 0-100% as you press/depress the pedal.

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

### Temperature Sensor Calibration

To calibrate the TPS, on the top of TunerStudio click on the Tools tab -> Calibrate Temperature Sensors.

Select Coolant Temperature Sensor and you will see a list of common sensors, as well as an option to provide a custom one.
If you have retained the factory coolant temperature sensor, you can select BMW E30 325i and then Write to Controller.

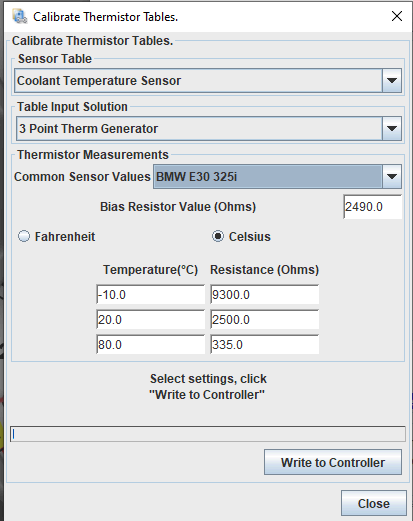
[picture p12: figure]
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

Now select Air Intake Temperature Sensor and you will see the same user interface.
If you have retained the factory air temperature sensor in the AFM, you can select BMW E30 325i and then Write to Controller.

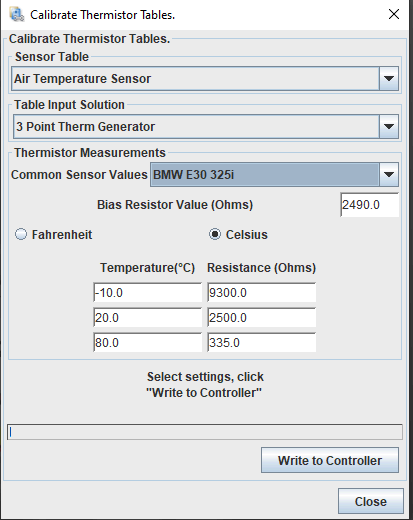
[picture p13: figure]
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

### Wideband Calibration

To calibrate the TPS, on the top of TunerStudio click on the Tools tab -> Calibrate AFR Sensor.

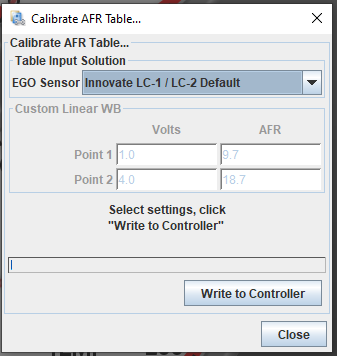
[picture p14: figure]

From the EGO sensor list, select the wideband controller you are using and click Write to Controller. If your wideband controller is not on the list, you should use the custom selection and manually enter the values according to the manufacturer's specification.

### Voltage Reading Calibration

The easiest method of calibrating your voltage reading is to use an accurate multimeter at the 12V input pin on the ECU connector (Pin 37) and adjusting the slider until the gauge in TunerStudio displays the expected value.

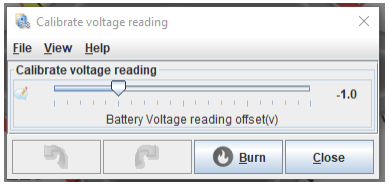
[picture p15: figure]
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

## Noteworthy Miscellaneous Items

### Getting Started with TunerStudio

Visit the following links for getting started with TunerStudio https://wiki.speeduino.com/en/Connecting_to_TunerStudio
Configuring TunerStudio project options | Speeduino Manual (https://wiki.speeduino.com/en/Configuring_TunerStudio)

### Firmware Updates

Speeduino undergoes continuous development, so make sure you keep checking in for firmware updates on the Speeduino website. It is recommended to use SpeedyLoader to update/load firmware and connect to your ECU via USB cable. It is also strongly recommended to unplug the ECU from your vehicle prior to updating the firmware as it may unexpectedly trigger certain outputs during the installation. After completing the update, double check your tune settings before starting your engine.
https://wiki.speeduino.com/en/Installing_Firmware

### Relay Outputs

Relay outputs on the Speeduino work via grounding.

### USB Connection

Make sure to use a USB 2.0 Type B cable for the ECU connection. It’s not recommended to use lengths over 5m to ensure there’s minimal interference. Depending on your vehicle, the straight connector cable provided with PNP kits may not clear. In those situations it may be required to purchase a separate 90 degree angle cable.

### Bluetooth

Please note that you cannot use USB and Bluetooth at the same time. To use USB you have to unpair the Bluetooth device and to use Bluetooth you must unplug the USB cable.
To connect your ECU via Bluetooth, the ECU must be connected to your vehicle and turned on via 12V. Using your PC/Tablet/Phone look for new Bluetooth devices. It will be called SPEEDUINO. Attempt to connect to it, and provide the PIN 3251.
On PC connections via Bluetooth, choose the appropriate COM port and tick the Bluetooth Port checkbox.
For more details please visit: https://wiki.speeduino.com/en/Bluetooth

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

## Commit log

2023-11-08 Adding v1 of assembly guide
2024-01-30 Updating User Guide
    Updating user guide steps outlining pinout for ECU connectors
2024-01-30 Adding Bill of materials file
    File contains individual component details
    [Motronic1-3_BOM.xlsx]
2024-09-09 Updating Assembly Guide
    Adding more verbose instructions about header pins on control boards
2024-10-15 Update Jetronic To Motronic Conversion.md
    adding diagrams and improving main relay wiring description
2024-10-21 Update Jetronic To Motronic Conversion.md
    adding details regarding blue coolant sensor
2024-11-13 Update Jetronic To Motronic Conversion.md
    adding reference image for welding trigger wheel to crank pulley
2025-01-08 adding VR conditioner production files and original KiCAD project files
    [V3_Conditioner_Kicad.kicad_pcb, V3_Conditioner_Kicad.kicad_sch, bom.csv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]

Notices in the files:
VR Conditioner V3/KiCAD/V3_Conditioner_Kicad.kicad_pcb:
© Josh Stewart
